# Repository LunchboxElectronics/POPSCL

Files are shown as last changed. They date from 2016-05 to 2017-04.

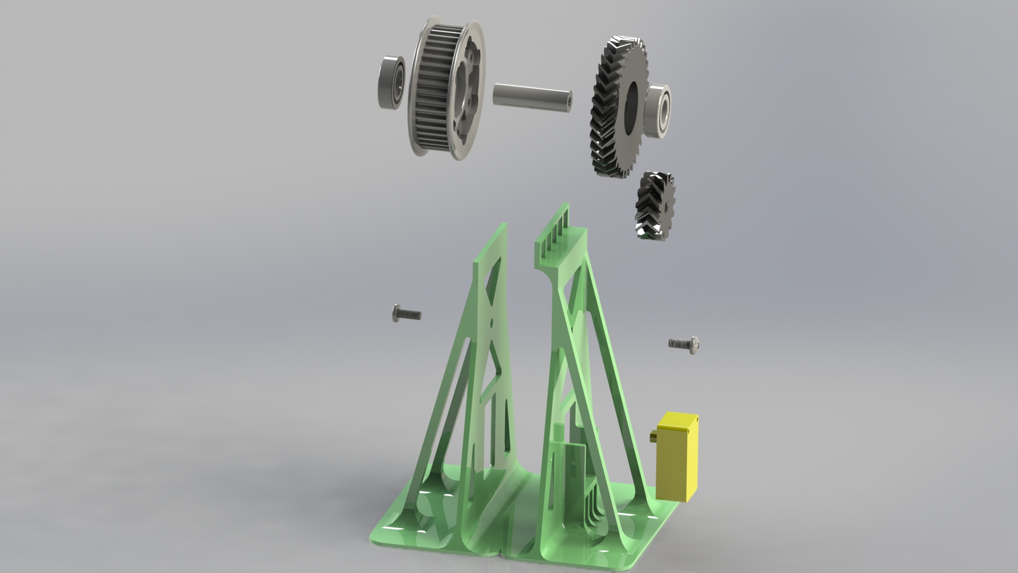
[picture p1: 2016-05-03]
ConveyorBeltParts/ConveyorbeltAexploded.JPG

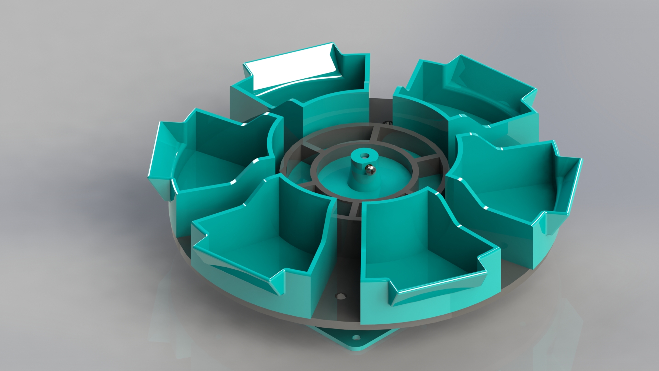
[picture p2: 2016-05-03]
CarouselParts/Carousel.JPG

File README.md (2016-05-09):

# POPSCL
Printed Open-Source Product Supply Counting Line -
This repository contains all the STL files needed to recreate Lunchbox Electronics Fulfillment Line POPSCL
In addition to the STL files:
STL files for the convayor belt pullies can be found here:
  http://www.andymark.com/product-p/am-2234.htm
STL files for the screws and nuts can be found here:
  http://www.mcmaster.com

All parts were printed on a Lulzbot Taz 5 with PLA or N-Gen filament

POPSCL was created to aid in the counting and packaging of Build Upons by Lunchbox Electronics. Instead of 
counting out a certain number of bricks and bagging them for hours, POPSCL will take bricks from a large
hopper and put them one by one onto a conveyor belt to be counted. These bricks are then dropped into a 
bucket to be dumped into a bag by the operator. 

The basic workflow of POPSCL is:
  1. A bunch of bricks get dumped into the hopper
  2. The cleated belt runs through the hopper picking bricks up one by one
  3. The cleated belt drops the individual bricks onto the prefeeder which is the transition to the conveyor belt.
  4. Once on the conveyor belt the bricks pass through a IR gate (this break of the IR beam is registered and each
brick is counted as it goes by)
  5. The bricks then fall off the conveyor belt in a bucket on the carousel
  6. When the determined number of bricks per bag is reached all motors stop and the carousel rotates to fill an
empty bucket with more bricks
  7. This process continues till there are no more bricks to bag

# Bill of Materials:
- All supplied 3D printed STL files
- Additional non-printed hardwear (per assembly)
  - Hopper
    - 2 #2-56 by 1/4" socket cap hex screws
    - 2 1.125" bearing (http://bit.ly/1Tkejrw purchased from Fastenal)
  - Prefeeder
    - 2 #2-56 by 1/4" socket cap hex screws
    - 1 1.125" bearing (http://bit.ly/1Tkejrw purchased from Fastenal)
  - Cleated Belt
    - L series timing belt, 24.8" outer circle (http://www.mcmaster.com/#6484k704/=128nk5q)
  - Conveyor Belt
    - 2 M5 by 1" machine screws
    - 2 M4 by 1" machine screws
    - 2 DC motors (sourced from Hummingbird Duo kit, http://www.hummingbirdkit.com/learning/duo-datasheet#fMotor)
    - STL files for 2 pullies from AndyMark (http://www.andymark.com/product-p/am-2234.htm)
    - HTD timing belt, 1,000mm outer circle (http://www.mcmaster.com/#7939k31/=128nldv)
    - IR emitter and IR detector (https://www.sparkfun.com/products/241)
    - 3 1.125" bearing (http://bit.ly/1Tkejrw purchased from Fastenal)
  - Carousel
    - 3 #4-40 by 1/4" machine screws
    - 3 #4-40 threaded inserts for plastic (http://www.mcmaster.com/#93365a120/=12964yt)
    - Stepper motor (https://www.sparkfun.com/products/9238)
    - Photocell (https://www.sparkfun.com/products/9088)
    - Half of a lulzbot filament reel
- Arduino
- Sparkfun Easydriver board
- Sparkfun Power Driver Shield Kit

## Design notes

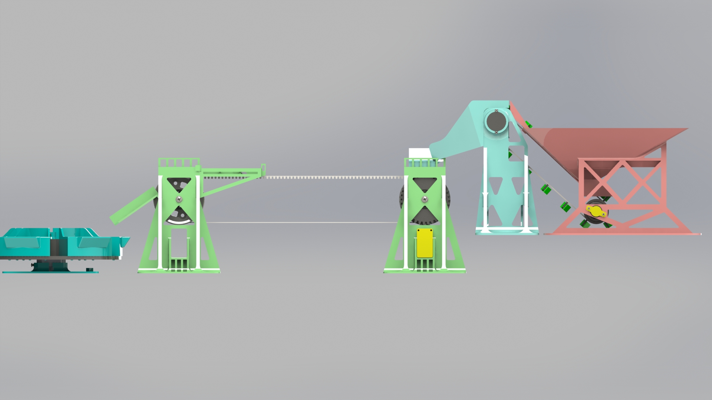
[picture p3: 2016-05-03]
POPSCL2.JPG

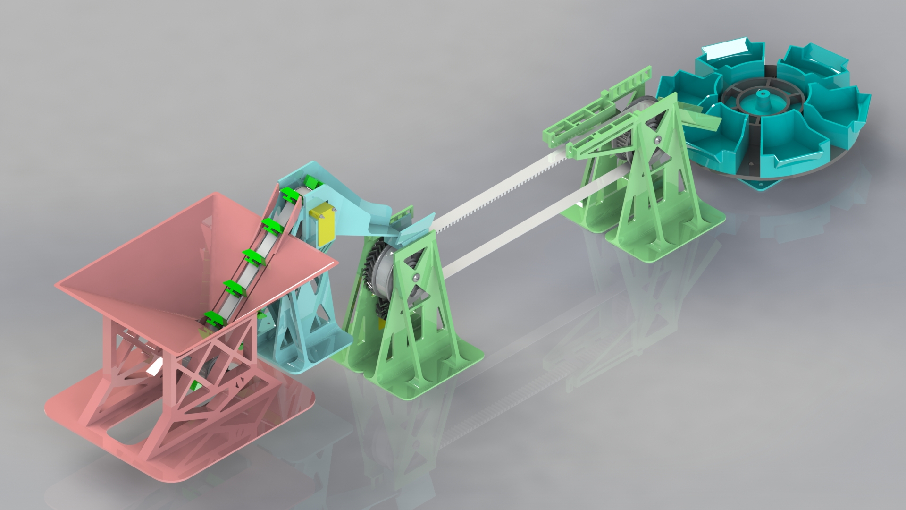
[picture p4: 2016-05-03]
POPSCL3.JPG

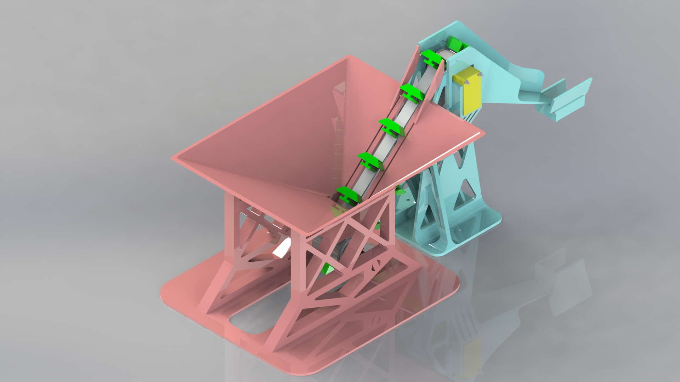
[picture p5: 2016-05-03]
HopperPrefeederCombo.JPG

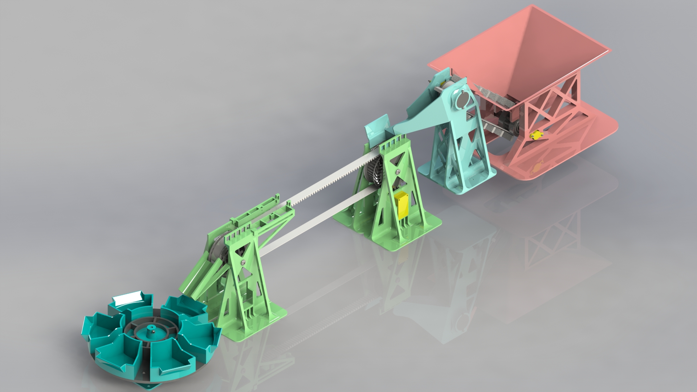
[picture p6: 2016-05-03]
POPSCL1.JPG

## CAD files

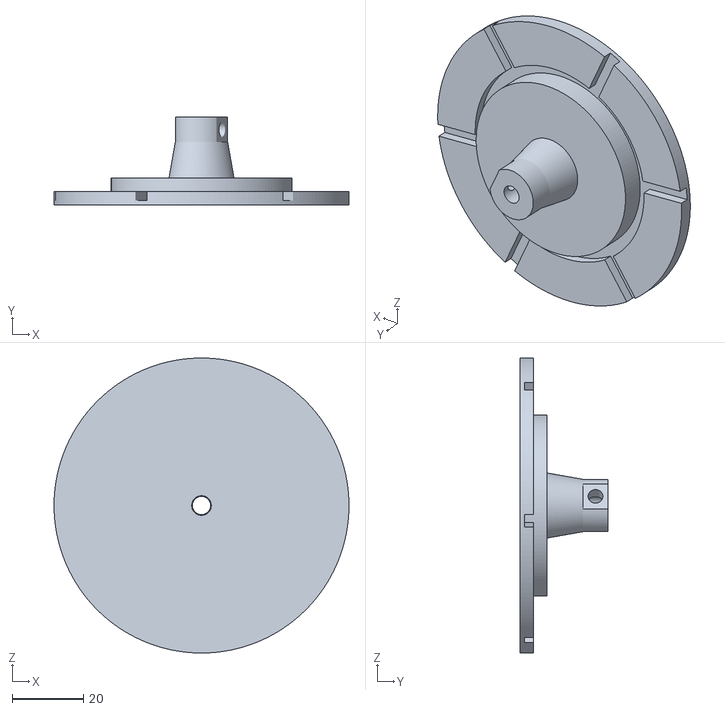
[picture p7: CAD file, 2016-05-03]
CarouselParts/CompleteFulfillmentLine - CarouselMount.STL
82.5 x 24.6 x 82.5

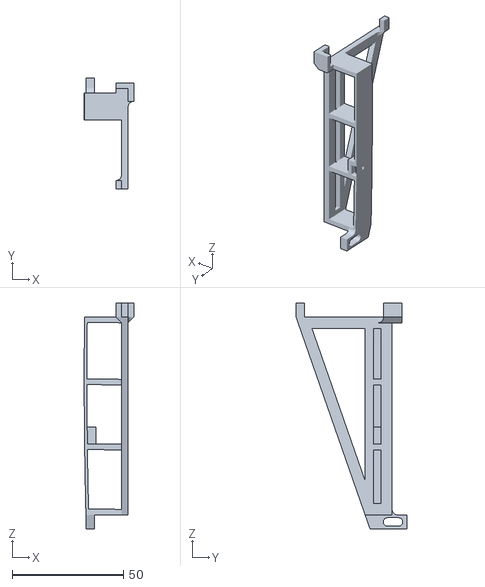
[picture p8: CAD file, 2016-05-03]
ConveyorBeltParts/CompleteFulfillmentLine - IRGateholder-2.STL
22.3 x 49.9 x 101.6

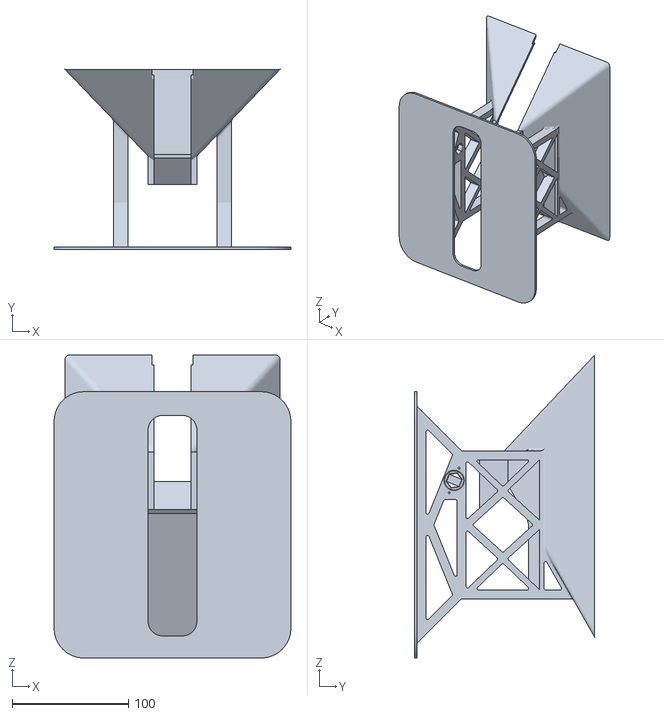
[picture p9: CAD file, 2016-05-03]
HopperParts/CompleteFulfillmentLine - Hopper.STL
203.2 x 154.9 x 260.1

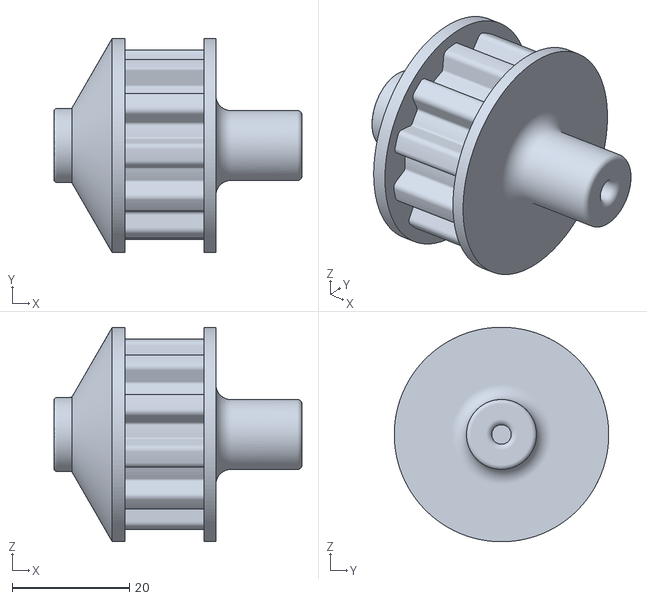
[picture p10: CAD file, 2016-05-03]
PrefeederParts/CompleteFulfillmentLine - CleatedBeltGearToMotor.STL
42.3 x 36.6 x 36.6

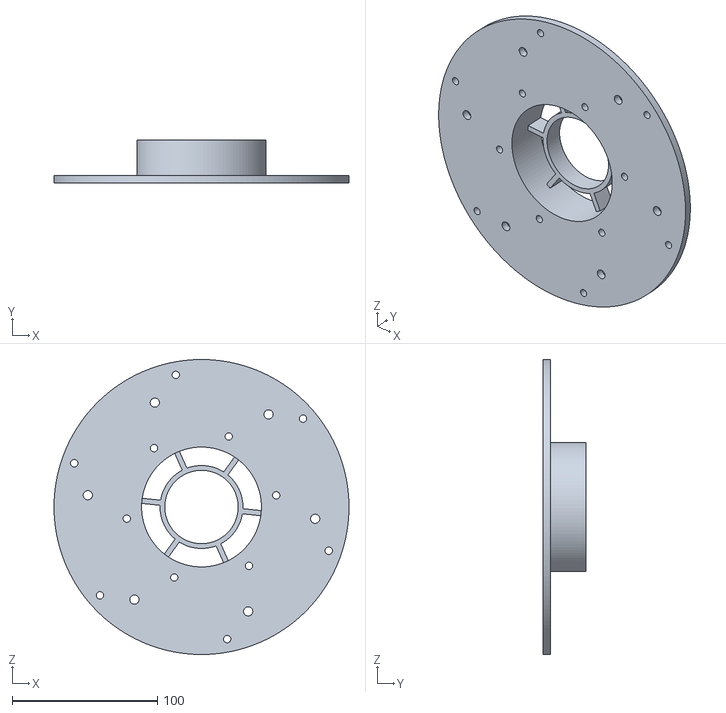
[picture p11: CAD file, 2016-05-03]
CarouselParts/CompleteFulfillmentLine - Carousel.STL
203.2 x 29.7 x 203.2

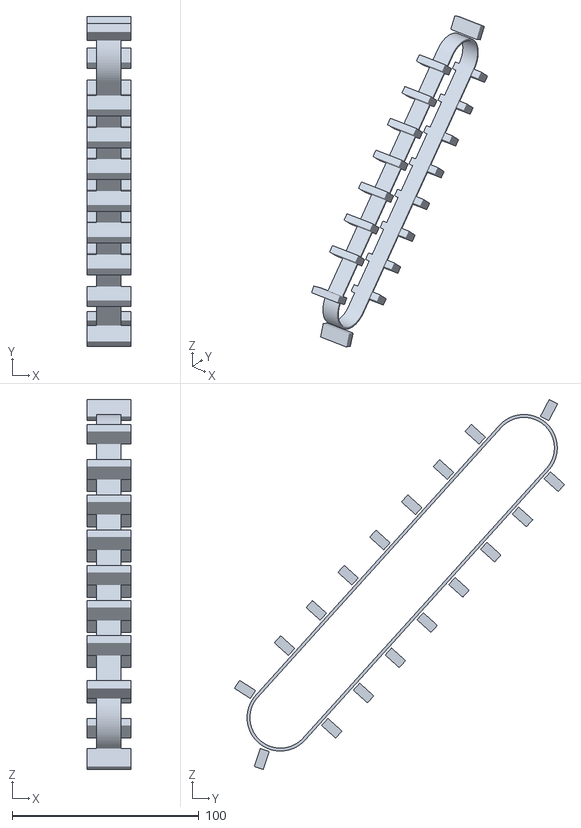
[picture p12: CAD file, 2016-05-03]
CleatedBeltParts/CompleteFulfillmentLine - CleatedBelt.STL
23.7 x 176.7 x 198.1

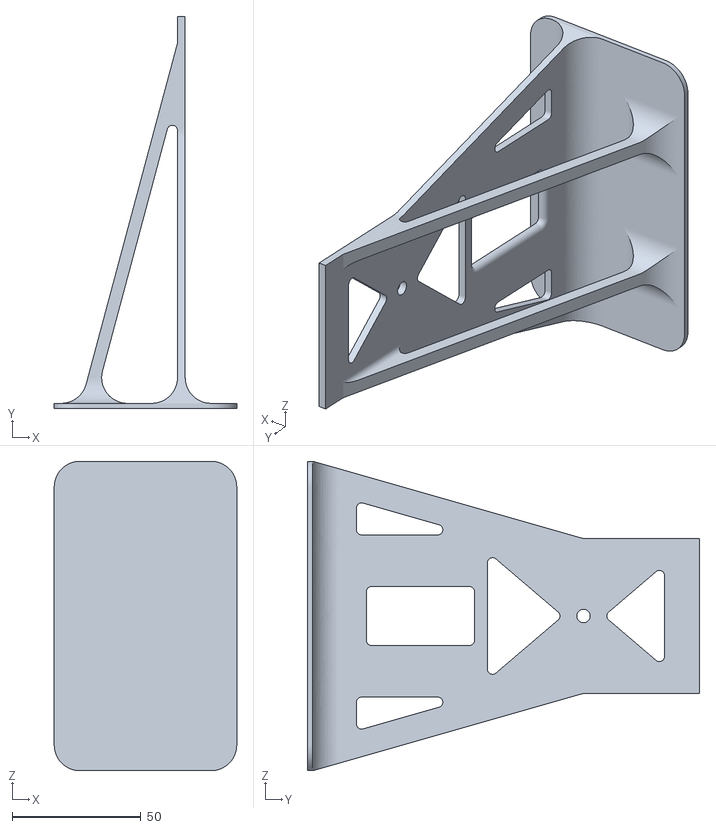
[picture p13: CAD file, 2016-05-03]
ConveyorBeltParts/CompleteFulfillmentLine - MotorStand-2.STL
70.8 x 152.0 x 120.0

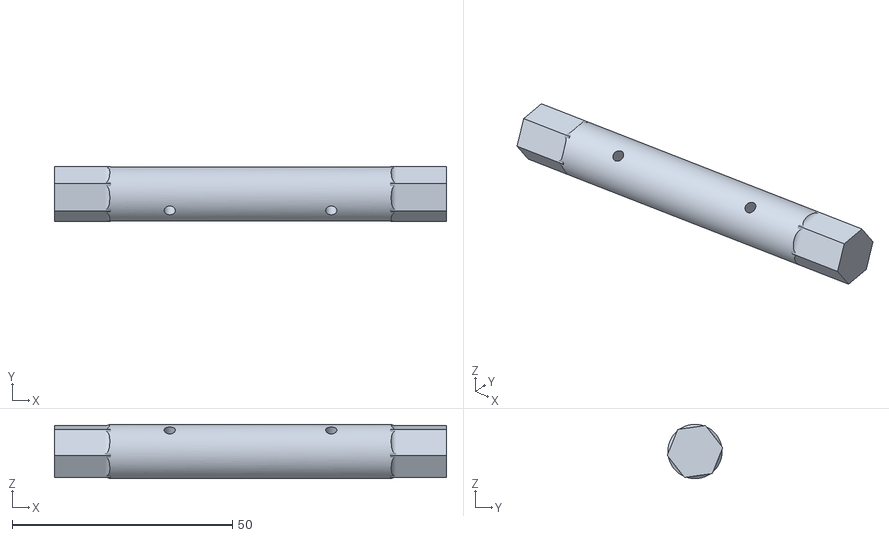
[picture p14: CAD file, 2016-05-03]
HopperParts/CompleteFulfillmentLine - HexShafthopper.STL
88.9 x 12.6 x 12.3

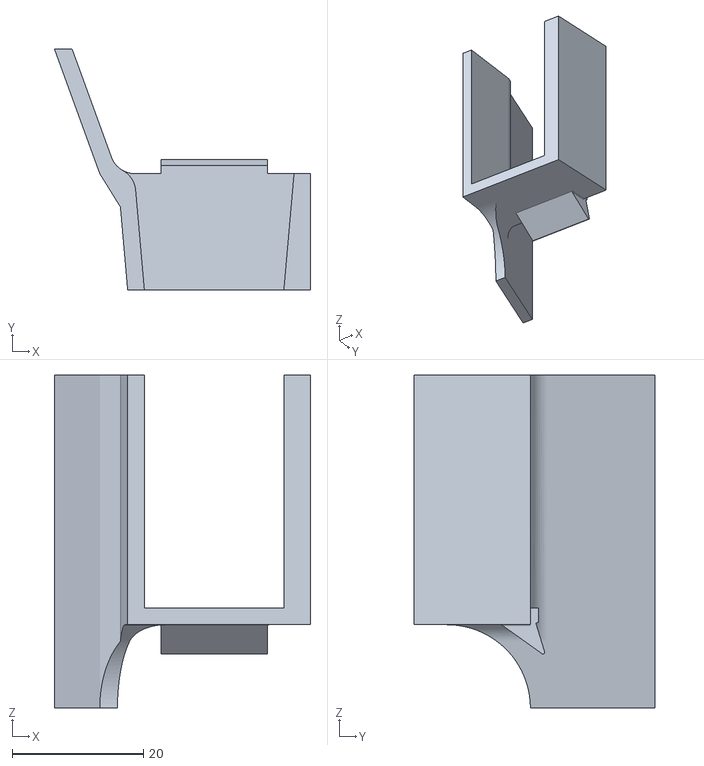
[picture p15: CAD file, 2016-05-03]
PrefeederParts/CompleteFulfillmentLine - backblocker.STL
39.1 x 36.8 x 50.8

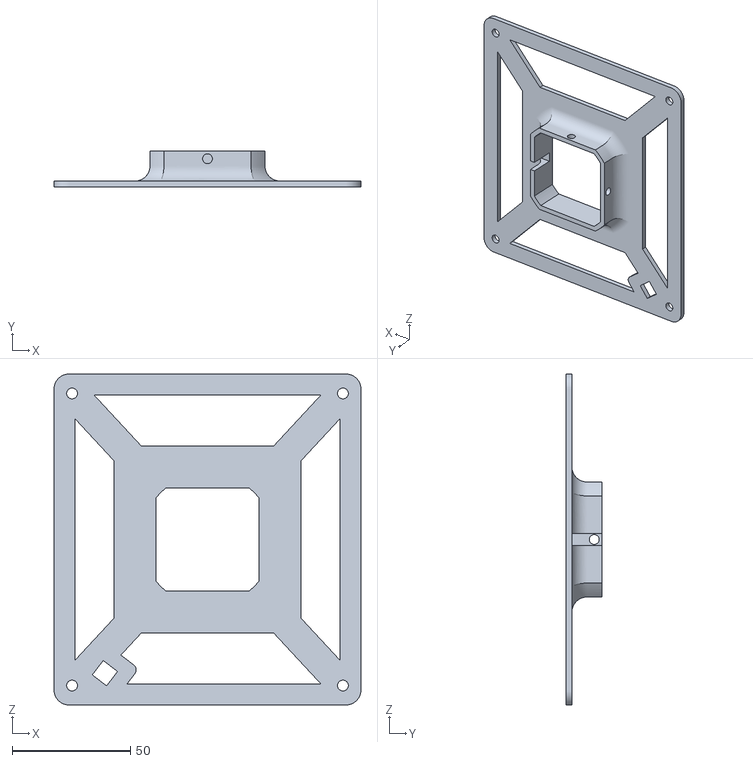
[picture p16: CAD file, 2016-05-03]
CarouselParts/CompleteFulfillmentLine - StepperMotorHolder.STL
129.5 x 15.2 x 139.7

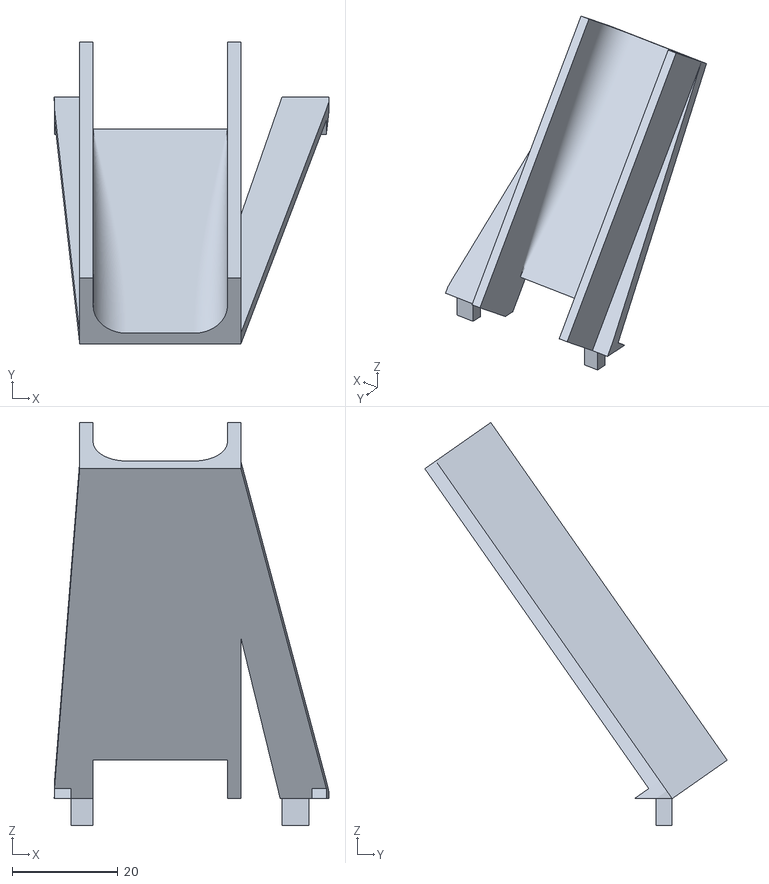
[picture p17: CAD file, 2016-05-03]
ConveyorBeltParts/CompleteFulfillmentLine - ExitSlide.STL
51.9 x 57.2 x 76.2

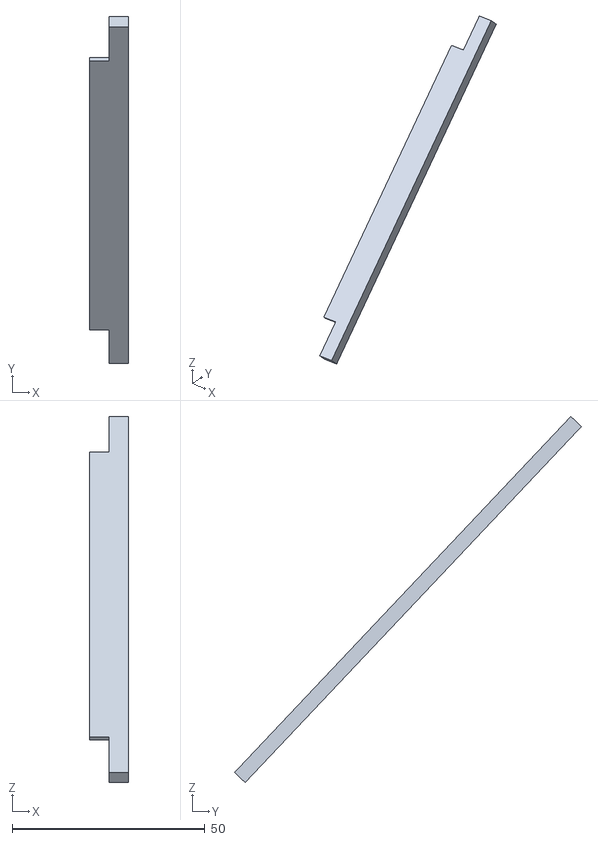
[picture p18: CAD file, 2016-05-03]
HopperParts/CompleteFulfillmentLine - Hopperplate.STL
10.2 x 90.0 x 94.9

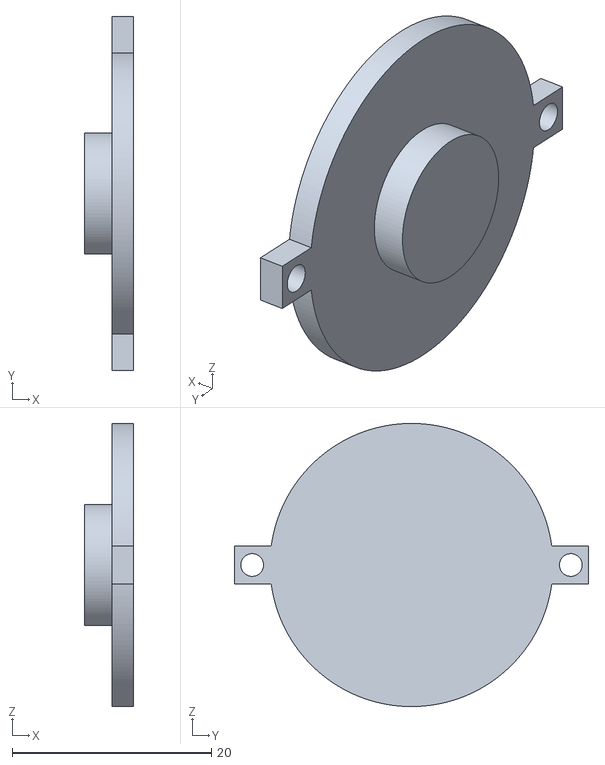
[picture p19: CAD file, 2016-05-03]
PrefeederParts/CompleteFulfillmentLine - BearingStop.STL
4.95 x 35.6 x 28.4

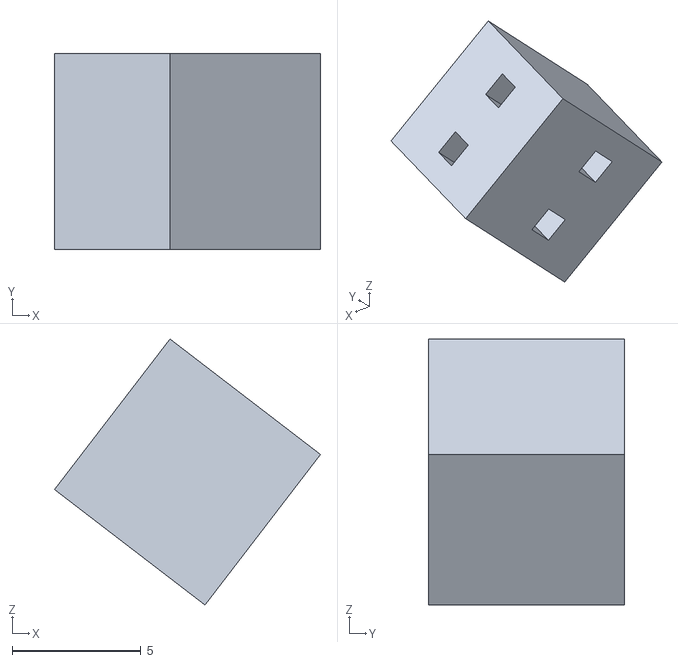
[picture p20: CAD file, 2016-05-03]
CarouselParts/CompleteFulfillmentLine - photoCellholder-1.STL
10.3 x 7.62 x 10.3

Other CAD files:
ConveyorBeltParts/CompleteFulfillmentLine - MockMotor.STL
HopperParts/CompleteFulfillmentLine - HopperHubcap.STL
PrefeederParts/CompleteFulfillmentLine - OrientationRamp.STL
CarouselParts/CompleteFulfillmentLine - bucket.STL
CleatedBeltParts/Cleat.STL
CleatedBeltParts/CleatBase.STL
ConveyorBeltParts/CompleteFulfillmentLine - Bridge.STL
ConveyorBeltParts/CompleteFulfillmentLine - HerringboneBase.STL
ConveyorBeltParts/CompleteFulfillmentLine - HerringboneToMotor.STL
ConveyorBeltParts/CompleteFulfillmentLine - IRGateholder-1.STL
ConveyorBeltParts/CompleteFulfillmentLine - MotorStand-1.STL
ConveyorBeltParts/CompleteFulfillmentLine - Shaft.STL
ConveyorBeltParts/CompleteFulfillmentLine - ShaftwCollar.STL
ConveyorBeltParts/CompleteFulfillmentLine - timingbelt2-1.STL
HopperParts/CompleteFulfillmentLine - CleatedBeltPulley.STL
HopperParts/CompleteFulfillmentLine - Guard.STL
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

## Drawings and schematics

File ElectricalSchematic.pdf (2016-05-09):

# System Ready LED Operating State Switch

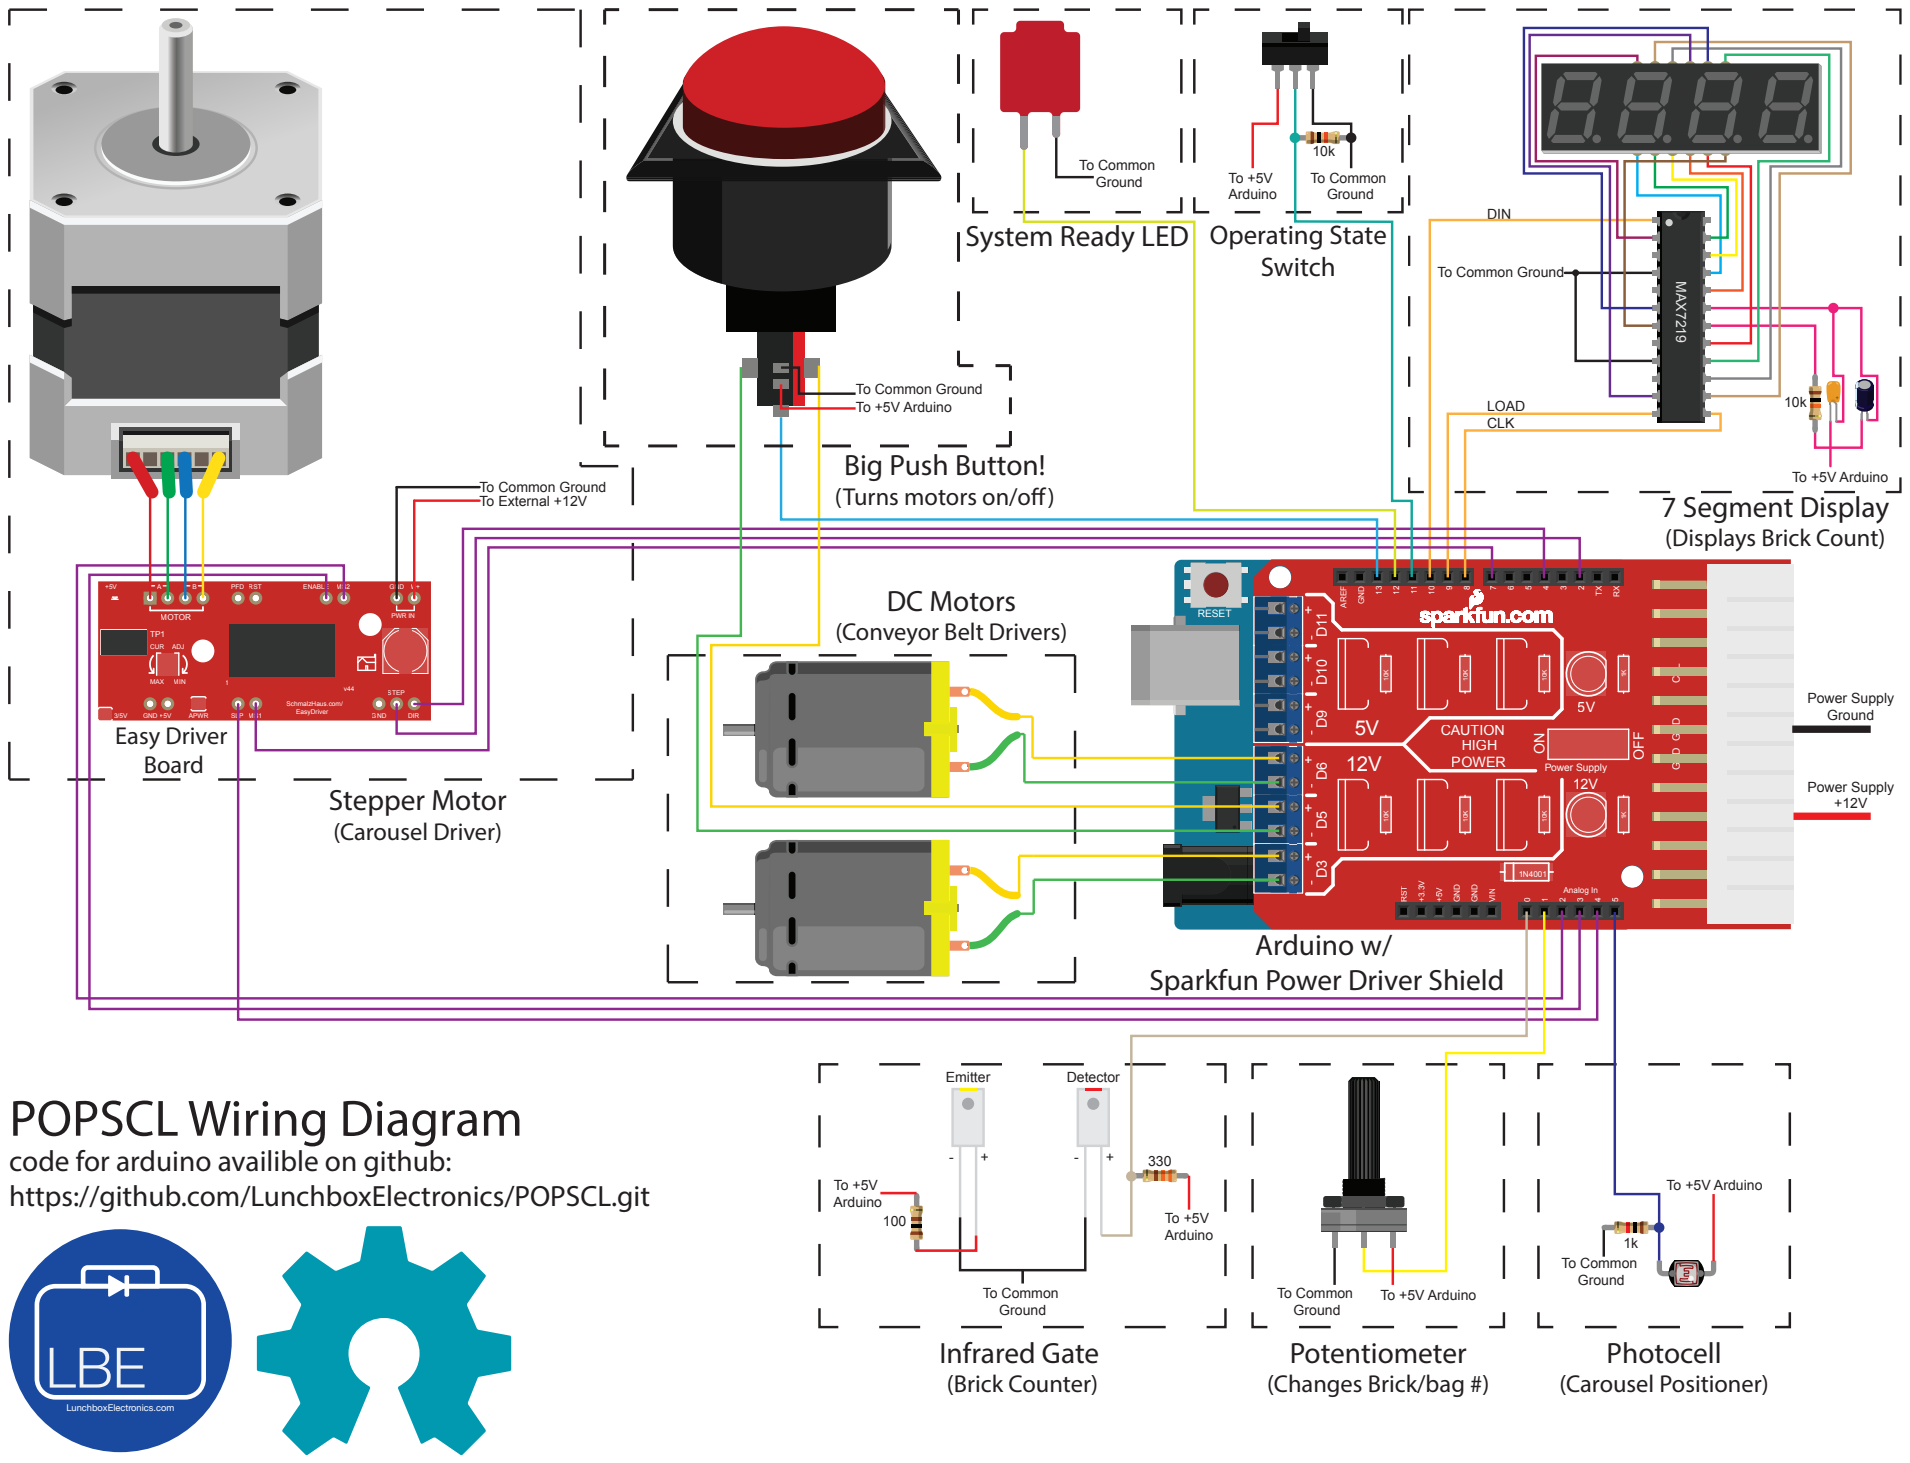
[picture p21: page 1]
ANALOG IN; AREF; GND; RESET; VIN; DIGITAL (PWM=; Arduino; IOREF; ICSP; ICSP2; POWER; DIR; EasyDriver; STEP; MOTOR; GND +5V; CUR; SLP MS1; PFD RST; ENABLE MS2; APWR; PWR IN; SchmalzHaus.com/; MAX MIN; ADJ; Power Supply +12V; Power Supply Ground; ATX Connector; CAUTION HIGH POWER; OFF; Power Supply; GND GND; GND 12V 12V; CTL; RST; Analog In; To External +12V; To Common Ground; To +5V Arduino; CLK; LOAD; DIN; MAX7219; Photocell (Carousel Positioner); Stepper Motor (Carousel Driver)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

To Common Ground

To +5V Arduino
Big Push Button!
(Turns motors on/o)

7 Segment Display
(Displays Brick Count)

(Conveyor Belt Drivers)

Arduino w/
Sparkfun Power Driver Shield

POPSCL Wiring Diagram
code for arduino availible on github:
https://github.com/LunchboxElectronics/POPSCL.git

To Common
Ground
Potentiometer
(Changes Brick/bag #)

LBE LunchboxElectronics.com

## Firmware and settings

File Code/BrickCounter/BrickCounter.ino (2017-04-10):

#include <LedControl.h>

/*Lunchbox Electronics 2016
 *Code to run an assembly line to automatically package Build Upons
 *The system uses two motors to run belts that move the bricks through the line
 *The bricks are counted with a IR sensor and then bagged for kitting
 *Created by Jason Brownstein
 */
 
#define stp 2                   // Defines stepper motor step pin
#define dir 4                   // Defines stepper motor direction pin
#define MS1 7                   // Defines stepper motor microstep1 pin
#define MS2 16                  // Defines stepper motor microstep2 pin, on analog in rail
#define EN  17                  // Defines stepper motor enable pin, on analog in rail
#define SLP 18                  // Defines stepper motor sleep pin, on analog in rail
int ledPin = 12;                // LED is connected to pin 12
int IRgate = 0;                 // IR gate is connected to pin A0
int val;                        // variable for reading the pin status
int newState;                   // variable to hold temp state status
int bricks = 0;                 // how many bricks have passed
int IRstate;                    // variable to hold the IR gate state
int offVal;                    // value when the gate is open
int onVal;                     // value when the gate is closed
int bagbricks = 3;             // variable for number of bricks per bag
int setpin = 11;                 // initiates the state to set number of bricks per bag mode
int setState;                   // variable to hold set number of bricks per bag state mode
int potpin = 1;                 // sets analog pin to read a potentiometer
int prefeederpin = 3;           // sets a pwm pin to control the motor speed on the prefeeder
int buttonpin = 13;             // set a digital pin to read the status of the big red button
int buttonState = 1;            // initiate the state of the button
int buttonlight = 5;           // LED in button is on digital pin 10
int convayorpin = 6;           // Convayor belt motor on digital pin 11
long timer = 0;                // Keep a reference time for prefeeder motor delay
long timer2;                   // Keep a second reference time for delay after bagbrick limit reached
bool limit = false;            // initiate a condition that bagbricks limit reached
int photopin = 5;              // define pin for photoresistor
int photo;
int prefeederspeed = 80;
int convayorspeed = 120;


LedControl counter = LedControl(10, 8, 9, 1);  // (DIN, CLK, LOAD, number of chips)

void setup() {
  Serial.begin(9600);                 // Set up serial communication
  counter.shutdown(0, false);         // turns on display
  counter.setIntensity(0, 5);        // 15 = brightest
  pinMode(ledPin, OUTPUT);            // Set the LED pin as OUTPUT
  pinMode(setpin, INPUT);             // set the set pin as INPUT to detect change
  setState = digitalRead(setpin);     // set initial state of mode switch counter or set # of bricks mode
  pinMode(prefeederpin, OUTPUT);      // set the pwm pin to OUTPUT
  pinMode(buttonpin, INPUT);          // set the button pin to INPUT to detect change
  pinMode(buttonlight, OUTPUT);       // set the button light pin to OUTPUT
  pinMode(convayorpin, OUTPUT);       // set the convayor belt pin to OUTPUT
  offVal = analogRead(IRgate);        // set initial reading base value of the IR gate
  onVal = offVal + 100;               // set threshold for level to be triggered when brick passes through
  pinMode(stp, OUTPUT);               // set all stepper motor pins to output
  pinMode(dir, OUTPUT);
  pinMode(MS1, OUTPUT);
  pinMode(MS2, OUTPUT);
  pinMode(EN, OUTPUT);
  pinMode(SLP, OUTPUT);
  resetEDPins();                      // Set step, direction, microstep and enable pins to default states
  digitalWrite(EN, LOW);              // set driver to enable stepper motor
  digitalWrite(SLP, HIGH);            // wake up stepper motor driver
  photo = analogRead(photopin);       // Read the photocell
  while(photo <= 100) {                // while the photocell reads low move the stepper motor
    //Serial.println(photo);
    runmotor();
  }
  delay(100);
  digitalWrite(SLP, LOW);             // sleep stepper driver to minimize power consumption
  printNumber(bricks);
  digitalWrite(ledPin, HIGH);         // Turn on led to indicate all is good
}

void loop() {
  //Serial.println(digitalRead(setpin));
  long currenttime = millis();
  if (digitalRead(setpin) == HIGH) {   // if the mode swtich is activated you can set
    Serial.println("oops");
    bricset();                           // the number of bricks per bag (when the counter cycles over)
  }
  // MOTOR INITIATOR AND KILL SWITCH
  if (digitalRead(buttonpin) == HIGH) {   // detect if the button has been pressed
    buttonState = -1 * buttonState;      // change the value of buttonState to show change
    delay(300);                          // add a delay to debounce button
    if (buttonState == -1) {               // case for button to initate motors
      analogWrite(prefeederpin, prefeederspeed);      // use analog write to drive a lower voltage to the prefeeder motor
      digitalWrite(buttonlight, HIGH);     // turn button light on
      analogWrite(convayorpin, convayorspeed);       // use analog write to drive a lower voltage to the convayor belt motor
      //digitalWrite(prefeederpin, HIGH);
      //digitalWrite(convayorpin, HIGH);
      return;
    }
    else {
      digitalWrite(prefeederpin, LOW);     // opposing case to kill the motors
      digitalWrite(convayorpin, LOW);
      digitalWrite(buttonlight, LOW);      // turn button light off
    }
  }
  //Serial.println(buttonState);
  if (buttonState == -1) {                 // If button is pressed start incremental step of prefeeder belt
    if (currenttime - timer > 200) {       // compare timers and turn off motor when greater than 200 ms
      digitalWrite(prefeederpin, LOW);
      if (currenttime - timer > 700) {     // compare times and turn motor back on 500ms after motor turned off
        analogWrite(prefeederpin, prefeederspeed);
        timer = currenttime;               // update the timer 
      }
    }
  }
  val = analogRead(IRgate);               // read input value and store it in val
  //Serial.println(val);
  // NO BRICK IS PRESENT IN THE GATE
  if (val < offVal) {                     // check if the analog value is less than the gate open threshold
    digitalWrite(ledPin, HIGH);           // turn LED on
    newState = 0;                         // update the state
  }
  // BRICK IS PASSING THROUGH THE GATE
  if (val > onVal) {                      // check if the analog value is greater than the gate closed threshold
    digitalWrite(ledPin, LOW);            // turn LED off
    newState = 1;                         // update the state
  }
  if (newState != IRstate) {              // check the state has changed
    if (val < offVal) {                   // if state has changed count brick once state goes back to open
      bricks++;                           // increment brick counter
      //Serial.println("+1");
      printNumber(bricks);                // feed brick count to the display for visual counting
    }
  if (bricks == bagbricks) {              // check if the brick count is over the bagbrick set number
    printNumber(bricks);                  // feed brick count to the display for visual counting
    timer2 = millis();
    limit = true;
    bricks = 0;                           // cycle over to recount for next bag
  }
  }
  if (currenttime - timer2 > 1025 && limit == true) {
    printNumber(bricks);
    digitalWrite(prefeederpin, LOW);      // code to stop motors for a duration
    digitalWrite(convayorpin, LOW);
    flashbutton();                        // flash button light for 2 sec so person can change to a new bag    
    }
  IRstate = newState;                     // save/update the new state in IRstate
}

// THIS WILL RESET THE VARIABLE BAGBRICKS WHEN SWITCH IS ACTIVATED
void bricset() {
  digitalWrite(prefeederpin, LOW);        // stop the motors if they were running
  digitalWrite(convayorpin, LOW);
  for ( int x = 1; x <= 1; x++) {     // initially scroll on display you are setting the brick count
    set();
    bric();
  }
  while (digitalRead(setpin) == HIGH) {
    bricks = 0;                         // clear brick count
    counter.clearDisplay(0);            // reset the display
    int val = analogRead(potpin);       // store the potentiometer signal to val
    val = map(val, 35, 1019, 0, 30);     // remap the pot values to our scale of 0 - 50 bricks
    printNumber(val);                   // call function to display any number on the display
    delay(500);
    bagbricks = val;                    // reset the variable bagbricks, will change where main loop counter cycles over
  }
  counter.clearDisplay(0);            // clear display to start fresh for counting again
  printNumber(bricks);
  return;
}


// MORE EFFICIENT WAY OF WRITING MULTIPLE CHARACTERS TO THE DISPLAY; Eberhard Fahle
// http://www.wayoda.org/arduino/ledcontrol/index.html
void printNumber(int bricks) {        // read in current brick value
  int brick = bricks;                 // define local variable brick
  int ones;
  int tens;
  int hundreds;
  boolean negative;

  if (brick < -999 || brick > 999)    // allow for range of -999 to 999 on display
    return;
  if (brick < 0) {                    // if less than zero make a negative number
    negative = true;
    brick = brick * -1;
  }
  ones = brick % 10;                  // find remainder of current brick value in each digit position
  brick = brick / 10;
  tens = brick % 10;
  brick = brick / 10;
  hundreds = brick;
  
  counter.setDigit(0, 1, (byte)hundreds, false);   //Now print the number digit by digit
  counter.setDigit(0, 2, (byte)tens, false);
  counter.setDigit(0, 3, (byte)ones, false);
}

//FUNCTION TO DISPLAY SET ON DISPLAY
void set() {
  counter.clearDisplay(0);
  counter.setDigit(0, 0, 5, false);  //S
  counter.setDigit(0, 1, 14, false); //E
  counter.setRow(0, 2, B00001111);   //t
  delay(2000);
}

//FUNCTION TO DISPLAY BRIC ON DISPLAY
void bric() {
  counter.clearDisplay(0);
  counter.setRow(0, 0, B00011111); //b
  counter.setRow(0, 1, B00000101); //r
  counter.setRow(0, 2, B00010000); //i
  counter.setRow(0, 3, B00001101); //c
  delay(2000);
}

//FUNCTION TO FLASH THE LED IN THE BUTTON
void flashbutton() {
  int temp = digitalRead(buttonlight);   //check if button light is on or not
  for (int x = 1; x < 3; x++) {          //loop twice to flash button
    digitalWrite(buttonlight, LOW);
    delay(200);
    digitalWrite(buttonlight, HIGH);
    delay(200);
  }
  digitalWrite(SLP, HIGH);              // wake up stepper motor driver
  delay(1);                             //delay for stability
  jogmotor();                           // move stepper an arbitrary amount to change photocell reading
  photo = analogRead(photopin);         // starting reading the photocell
  while(photo <= 50){                   // while photocell is in dark run stepper motor
    runmotor();                         // effectively moves to next bucket
  }
  delay(500);                           // add a half second pause for smoother transition
  digitalWrite(SLP, LOW);               // sleep stepper motor driver
  if (temp == 0) {                      // if button was off turn it back off
    digitalWrite(buttonlight, LOW);
  }
  if (buttonState == -1) {              // if button state had been "motors on" turn convayor back on
    analogWrite(convayorpin, convayorspeed);
  }
  limit = false;                        // reset limit boolean
}

//Reset Easy Driver pins to default states
void resetEDPins()
{
  digitalWrite(stp, LOW);              
  digitalWrite(dir, LOW);
  digitalWrite(MS1, LOW);
  digitalWrite(MS2, LOW);
  digitalWrite(EN, HIGH);
}

// RUN STEPPER MOTOR FORWARDS TILL NEXT BUCKET (based on photoresistor reading)
void runmotor(){
  digitalWrite(dir, HIGH);   //move "forward"
  digitalWrite(MS1, HIGH);  // High MS1 and High MS2 is 1/8 step
  digitalWrite(MS2, HIGH);
  //STEP TRIGGER
  digitalWrite(stp, HIGH);  //trigger one step forward
  delay(1);
  digitalWrite(stp, LOW);   //pull step pin low so it can be triggered again
  delay(1);
  photo = analogRead(photopin);   //reread photocell to update while condition
}

// JOG STEPPER MOTOR FORWARDS 100/8 steps
void jogmotor(){
  digitalWrite(dir, HIGH); //move "forward"
  digitalWrite(MS1, HIGH);  // High MS1 and High MS2 is 1/8 step
  digitalWrite(MS2, HIGH);
  for (int x= 1; x < 100; x++) {
    digitalWrite(stp, HIGH); //trigger one step forward
    delay(1);
    digitalWrite(stp, LOW); //pull step pin low so it can be triggered again
    delay(1);
  }
}

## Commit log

2016-05-03 Added initial Files
    Enjoy!
    [Cleat.STL, CleatBase.STL, CompleteFulfillmentLine - BearingStop.STL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]
2016-05-09 Updated Documentation
    [CompleteFulfillmentLine - Bridge.STL, CompleteFulfillmentLine - ExitSlide.STL, CompleteFulfillmentLine - HerringboneBase.STL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]
2017-04-10 Changed some speed parameters
    Slowed down the conveyor speeds to work smoothly with the bridge brick
    shape.
